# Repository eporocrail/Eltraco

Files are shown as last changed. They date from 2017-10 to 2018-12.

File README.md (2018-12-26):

  Aim is to develop a switching and signaling system for model railroad track control.
  Communication is wireless.

  To disconnect the decoder from the controlling software in space and time the MOSQUITTO
  MQTT broker is used.

  Hardware setup is as simple as possible. In stead of having one hardware module for diffferent applications
  the design aims for three different PCB's specific to task where the Wemos has to be slotted into.

  Sofware is modularised. It is gathered into one software package. The functionality of each separate decoder
  is configured by means of a website genrated by the decoder.

  *********************************************************************************************

  Target platform is Wemos D1 mini.

  11 digital input/output pins, all pins have interrupt/pwm/I2C/one-wire supported(except D0)
  1 analog input(3.2V max input)
  a Micro USB connection
  compatible with Arduino IDE.
  pins are active LOW but the Arduino IDE inverts this.

  All of the IO pins run at 3.3V:
  A levelshifter or voltage divider is required.

  For a relay a pin is followed by a transistor/IC. A relay is driven with 5V.

  For a sensor or servo each pin is followed by a 330R resistor to limit current to 10 mA.

  eltraco decoder     Function

  eltraco sensor decoder    Scanning 9 sensors
  eltraco switch decoder    Controlling 8 outputs
  eltraco turnout decoder   Controlling 2 turnouts

  GPIO usage:

  Decoder  pins     function

  Sensor   D0 .. D7     digital sensor
  
           A0           analogue sensor

  Switch   D0 .. D7     output (switch)

  Double   D0    relais 1
  
  Turnout  D1    current detector 1
           
           D2    current detector 2
           
           D3    not used
           
           D4    not used
           
           D5    relais 2
           
           D6    servo 1
           
           D7    servo 2
           
           D8    not used
           
           A0    not used
           
  Single   D0    relais 1
  
  Turnout  D1    current detector 1
           
           D2    sensor
           
           D3    sensor
           
           D4    sensor
           
           D5    sensor
           
           D6    servo 1
           
           D7    not used
           
           D8    not used
           
           A0    not used         

  ROCNET PROTOCOL

  packet payload content:
  byte 1  : groupId
  
  byte 2  : receiveIdH
  
  byte 3  : receiveIdL
  
  byte 4  : sendIdH
  
  byte 5  : sendIdL
  
  byte 6  : group
  
  byte 7  : code
  
  byte 8  : length
  
  byte 9  : data1
  
  byte 10 : data2
  
  byte 11 : data3
  
  byte 12 : data4

  --byte 1 only used for large network. Normally 0.

  --byte 2 only used when more than 255 decoders. Normally 0.

  --byte 3 Rocrail Server default Id is 1

  Broadcast Id = 0
  
  Decoder   Id = 2 ... 255   Not used for switching decoder

  --byte 4 only used when more than 255 decoders. Normally 0.

  --byte 5 Rocrail Server default Id is 1

  Decoder Id   = 2 ... 255 with restrictions as described under "addressing"

  --byte 6

  groups
  code   description     remark                     MQTT topic
  
  0      Host            Rocrail                    rocnet/ht
  
  7      Clock Fast      Clock                      rocnet/ck
  
  8      Sensor          Position determination     rocnet/sr
  
  9      Output                                     rocnet/ot

  --byte 7

  Code:  bit 7 = 0
  
     bit 6 and bit 5 represent Type of code
     
     bit 4 .. 0:  5 bit command 0 .. 31

  Type: 0 - test
  
  1 - request
  
  2 - event
  
  3 - reply

  Sensor

  Actions
  code description data 1  data 2  data 3  data 4  data n
  1    report      addrH¹  addrL¹  status  port    identifier (RFID)

  ¹) Address of the reporting loco.
  The sensor ID is set in the header; Sender.

  Output

  Type   Value
  
  switch   0
  
  light    1
  
  servo    2

  Actions
  code description data 1  data 2  data 3
  
  0      off       type    value   address
  
  1      on        type    value   address

  --byte 8 Netto number of following data bytes.

  At a speed of 200 KmH a loc runs 64 mm per second in scale H0 and 35 mm per second in scale N.
  To come to a reliable detection reaction a point sensor must be scanned at least 20 times per second in H0
  and at least 10 times per second in scale N.

  For scale H0 scan delay should be not larger than 50 miliseconds and for scale N not larger
  than 100 miliseconds. Default will be 20.

  The Wemos Module needs no 3.3V power supply. To the 5V pin external powersupply can be connected.

  Addressing:

  Addressing falls apart in a WiFi address, being an IP-address and a Rocnet address.

  Rocnet:

  In the Rocnet protocol (IdH*256 + IdL) represents the Rocnet Node Number. This number ranges from 1 .. 65536.
  It represents the "Bus" number.
  Depending on the function performed the I/O pin of the decoder is addressed with "data3" for
  "output" functions or "data4" for "sensor" functions. Turnouts are controlled with an "output" function.
  The values of data3/data4 are in rocrail inserted in field "Address"

  For eltraco an I/O pin is addressed by the combination of receiveIdL and data3/data4.
  This way each individual pin of each individual decoder can be addressed.

  A second way to address an IO pin is using a "fixed" receiveIdL and discriminating by means of data3/data4.
  Using this method provides in eltraco the possibility to address 255 turnouts by a consecutive number only.
  The default receiveIdL of Rocrail is "9". This receiveIdL is used to control turnouts. These addresses are
  used by the servo-tool to adjust the servo of a turnout.

  IP-address:
  The following IP-adress range is available:
  192.168.xxx.xxx

  IP-addres: Router 192.168.xxx.251
  
             Configuration website 192.168.xxx.252
             
             Command Station       192.168.xxx.253
             
             Mosquitto             192.168.xxx.254

  For the decoders are available 192.168.xxx.2 - 192.168.2.250

  Each decoder is allocated a unique IP-address out of the range 192.168.xxx.2 - 192.168.2.250.
  The last triplet is the Rocrail "Bus" number.

  Single turnout decoder:

Each decoder controls 1 turnout and reports occupation of it.

For the turnout decoder occupation of the turnout is reported at "Address" 1.

Table: Switches tab Interface - the last part of the IP-address is inserted into field "Bus"
       "1" is inserted into field "Address".
       e.g. (192.168.0.154 turnout is inserted as Bus 154 Address 1)

Table: Sensor tab Interface - the last part of the IP-address is inserted into field "Bus"
       "1" is inserted into field "Address". The external sensors report using "Address" numbers 2 .. 5.
       e.g. (192.168.0.154 turnout is inserted as Bus 154 Address 1, the second external sensor of the same
       decoder is inserted as Bus 154 Address 3)

Double turnout decoder:

Each decoder controls 2 turnouts and reports occupation of them.

For the turnout decoder occupation of the first turnout is reported at "Address" 1 and of the second
turnout at "Address" 2.

Table: Switches tab Interface - the last part of the IP-address is inserted into field "Bus"
       For the first turnout "1" is inserted into field "Address". For the second one "2" is inserted
       e.g. (192.168.0.154 turnout 2 is inserted as Bus 154 Address 2)

Table: Sensor tab Interface - the last part of the IP-address is inserted into field "Bus"
       For the first turnout "1" is inserted into field "Address". For the second one "2" is inserted
       e.g. (192.168.0.154 turnout 2 is inserted as Bus 154 Address 2)

Operation

During testing it turned out that move orders from Rocrail arrived so fast that an ongoing movement was
interrupted. To cater for this, incoming turnout orders are stored into a buffer. When ongoing movement is concluded,
buffer content is converted into a turnout order and the next turnout starts moving.

Sensor decoder:
Each decoder has eight digital and one analogue sensor.

The sensors report using "Address" numbers 1 .. 9.
Use of the analogue sensor is to be programmed by the user.

Table: Sensor tab Interface - the last part of the IP-address is inserted into field "Bus"
       port number is inserted into field "Address"
       e.g. (192.168.0.076 sensor 5 is inserted as Bus 76 Address 5)

Operation

The state of the sensor is controlled by interrupt. Not only the state of the sensor but also the point in time of activation is stored.
If the sensor is still in the activated state after the debounce period has passed the Sensor Message is sent. 
The state of the sensor will change to "inactive" by interrupt. After the minimum activation time has passed this inactive state is signalled 
with a Sensor Message.

Interrupt reacts on changes to drive the sensor state.

D0 can NOT be used with Interrupt. This reduces the amount of interrupt driven sensors per module to 7. (D1 .. D7).

D0 has to be watched with "polling".

Switch decoder
Each decoder has eight outputs.

Each decoder is allocated a unique IP-address out of the range 192.168.xxx.2 - 192.168.2.250.
The last triplet is the Rocrail "Bus" number.

The outputs are switched using "Address" numbers 1 .. 8.

Table: Switches tab Interface - the last part of the IP-address is inserted into field "Bus"
       The individual port number is inserted into field "Address"
       e.g. (192.168.0.201 port 3 is inserted as Bus 201 Address 3)

Operation

Via configuration it is possible to have an output switched ON during 200 mSec. An additional relais attached to that
output can be used to control a solenoid activated device.

To signal the state of a switch, a sensor message is transmitted after each switch action. 

Configuration of decoder

The Wemos module can be used in "ST" mode and "AP" mode simultaneously.
In "ST" mode it is possible to login onto an existing WiFi network for normal operations.
In "AP" mode it is possible to generate its own WiFi network. This network is used for configuration of the decoder.
Each module has its own configuration webserver on a shared WiFi configuration network with its own IP address.

The websever is based on the "EmbAJAX" library. This library facilitates dataexchange between webserver on the decoder
and a browser on a client. The user experience is as much as possible comparable with webservers on PC like hardware.

Configuration data and servo angles are stored in EEPROM.
Allocation of EEPROM memory to variables has to be planned.
  location variable
      0    AngleA1
      1    AngleB1
      2    Delay1
      3    Swap1
      4    AngleA2
      5    AngleB2
      6    Delay2
      7    Swap2
      8    decoderType
      9    debugFlag

  GENERALOFFSET+ 0 .. 25 ST WiFi SSID
  
  GENERALOFFSET + SSIDOFFSET + 0 .. 8 ST WiFi Password
  
  GENERALOFFSET + SSIDOFFSET + PWDOFFSET + 0 .. 6 ST WiFi IP address triplets
  
  GENERALOFFSET + SSIDOFFSET + PWDOFFSET + IPOFFSET + 0 .. 8 Output puls 
  
  GENERALOFFSET + SSIDOFFSET + PWDOFFSET + IPOFFSET + OUTPUTOFFSET + 0 .. 8 Switch active puls length
  
  GENERALOFFSET + SSIDOFFSET + PWDOFFSET + IPOFFSET + OUTPUTOFFSET + PULSLENGTHOFFSET+ 0 .. 8 Output sensor message

  GENERALOFFSET      - 20
  SSIDOFFSET         - 30
  PWDOFFSET          - 20
  IPOFFSET           - 10
  OUTPUTOFFSET        -10
  PULSLENGTHOFFSET    -20
  OUTPUTSENSOROFFSET  -10

The ST WiFi password is generated out of "ELTRACO" and the decoderId.
The AP WiFi SSID is generated out of "ELTRACO" and the decoderID. This also aplies to the related password.

There are two ways to transfer Software to the decoder.
Via USB cable and after inital software installation also "Over The Air"(OTA).
Each decoder has its own OTA name which is generated outof "ELTRACO" and the decoderId.

Author: E. Postma

November 2018

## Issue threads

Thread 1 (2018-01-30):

Where is  "user_interface.h"?

dagnall53, 2018-01-30:
The code for the servo setting tool looks very interesting, but I missed / cannot find "user_interface.h"
Can you add it to the repository or add a note to say where it is?
Many thanks
Dagnall

eporocrail, 2018-01-31:
Dagnall,
Thanks for the remark. You got me! It is a remnant which needs to be done away with.
I am working on a new version of the software, one single software package for all types of decoder. In that version it is not present anymore.
Ellard

Closed 2018-01-31.

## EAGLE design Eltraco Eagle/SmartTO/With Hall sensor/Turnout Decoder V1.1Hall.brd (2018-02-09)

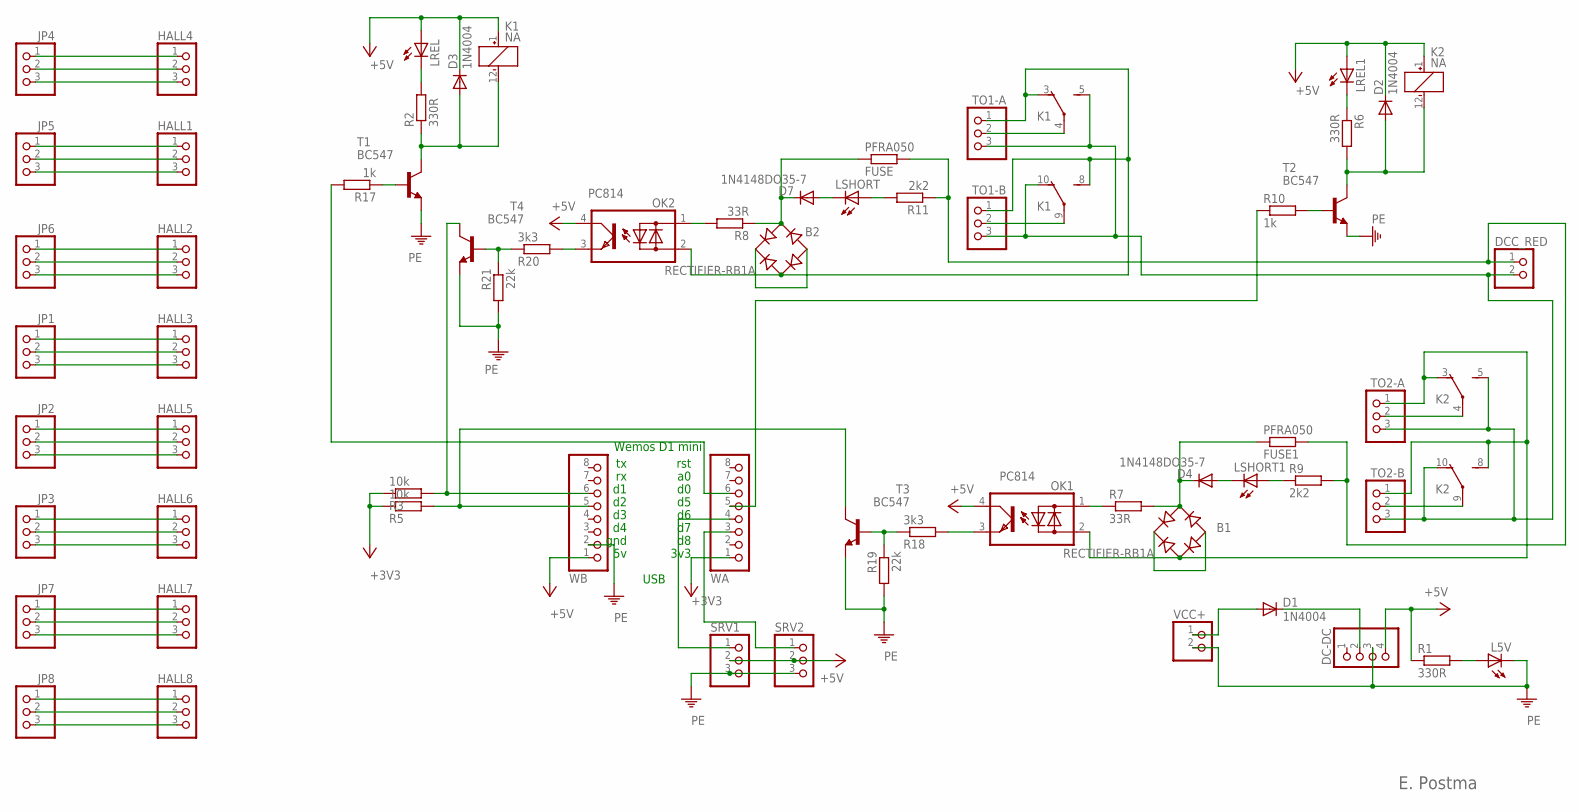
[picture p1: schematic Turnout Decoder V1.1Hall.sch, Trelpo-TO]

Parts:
B1, B2: RECTIFIER-RB1A; RB1A
D1, D2, D3: 1N4004; DO41-10
D4, D7: 1N4148DO35-7; DO35-7
DC-DC: PINHD-1X4; 1X04
DCC_RED: PINHD-1X2; 1X02
FUSE, FUSE1: PFRA050; 0414V
HALL1, HALL2, HALL3, HALL4, HALL5, HALL6, HALL7, HALL8: PINHD-1X3; 1X03
JP1, JP2, JP3, JP4, JP5, JP6, JP7, JP8: PINHD-1X3; 1X03
K1, K2: NA
L5V: LED3MM
LREL, LREL1: LED3MM
LSHORT, LSHORT1: LED3MM
OK1, OK2: PC814; DIL04
R1, R2, R6: 330R; 0207/7
R3, R5: 10k; 0207/7
R7, R8: 33R; 0207/7
R9, R11: 2k2; 0207/7
R10, R17: 1k; 0207/7
R18, R20: 3k3; 0207/7
R19, R21: 22k; 0207/7
SRV1, SRV2: PINHD-1X3; 1X03
T1, T2, T3, T4: BC547; TO92
TO1-A, TO1-B, TO2-A, TO2-B: PINHD-1X3; 1X03
VCC+: PINHD-1X2; 1X02
WA: PINHD-1X8; 1X08
WB: PINHD-1X8; 1X08

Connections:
+3V3: R3.1, R5.1, WA.1
+5V: D2.C, D3.C, DC-DC.4, K1.1 (+), K2.1 (+), LREL.A, LREL1.A, OK1.4 (C), OK2.4 (C), R1.1, SRV1.2, SRV2.2, WB.1
unnamed: HALL1.2, JP5.2
unnamed: LREL1.K (C), R6.1
unnamed: DCC_RED.1, FUSE.2, FUSE1.2, R9.2, R11.1
unnamed: D1.A, VCC+.1
unnamed: OK1.1 (AC1), R7.1
unnamed: LSHORT1.A, R9.1
unnamed: D4.A, LSHORT1.K (C)
unnamed: D2.A, K2.12 (-), R6.2, T2.3 (C)
unnamed: R10.2, T2.2 (B)
unnamed: B1.+, B1.-
unnamed: OK1.3 (E), R18.2
unnamed: LREL.K (C), R2.2
unnamed: K2.4, TO2-A.2
unnamed: B2.AC2, K1.3 (O), K1.8 (S), OK2.2 (AC2), TO1-A.1, TO1-B.1
unnamed: K2.9, TO2-B.2
unnamed: DCC_RED.2, K1.5 (S), K1.10 (O), K2.5 (S), K2.10 (O), TO1-A.3, TO1-B.3, TO2-A.3, TO2-B.3
unnamed: OK2.3 (E), R20.2
unnamed: B1.AC2, K2.3 (O), K2.8 (S), OK1.2 (AC2), TO2-A.1, TO2-B.1
unnamed: R3.2, T4.3 (C), WB.6
unnamed: B1.AC1, D4.C, FUSE1.1, R7.2
unnamed: OK2.1 (AC1), R8.2
unnamed: R5.2, T3.3 (C), WB.5
unnamed: B2.AC1, D7.C, FUSE.1, R8.1
unnamed: HALL1.1, JP5.1
unnamed: HALL1.3, JP5.3
unnamed: K1.4, TO1-A.2
unnamed: R18.1, R19.1, T3.2 (B)
unnamed: R20.1, R21.1, T4.2 (B)
unnamed: R17.2, WA.6
unnamed: HALL2.2, JP6.2
unnamed: SRV1.1, WA.4
unnamed: K1.9, TO1-B.2
unnamed: SRV2.1, WA.3
unnamed: R10.1, WA.5
unnamed: LSHORT.A, R11.2
unnamed: HALL2.1, JP6.1
unnamed: HALL2.3, JP6.3
unnamed: HALL3.2, JP1.2
unnamed: HALL3.1, JP1.1
unnamed: HALL3.3, JP1.3
unnamed: D7.A, LSHORT.K (C)
unnamed: B2.+, B2.-
unnamed: HALL5.2, JP2.2
unnamed: HALL5.1, JP2.1
unnamed: HALL5.3, JP2.3
unnamed: L5V.A, R1.2
unnamed: HALL6.2, JP3.2
unnamed: HALL6.1, JP3.1
unnamed: R17.1, T1.2 (B)
unnamed: D3.A, K1.12 (-), R2.1, T1.3 (C)
unnamed: HALL6.3, JP3.3
unnamed: HALL7.2, JP7.2
unnamed: HALL7.1, JP7.1
unnamed: HALL7.3, JP7.3
unnamed: HALL4.2, JP4.2
unnamed: HALL4.3, JP4.3
unnamed: HALL4.1, JP4.1
unnamed: D1.C, DC-DC.2
unnamed: HALL8.2, JP8.2
unnamed: HALL8.1, JP8.1
unnamed: HALL8.3, JP8.3
PE: DC-DC.3, L5V.K (C), R19.2, R21.2, SRV1.3, SRV2.3, T1.1 (E), T2.1 (E), T3.1 (E), T4.1 (E), VCC+.2, WB.2

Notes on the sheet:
rst
3v3
Wemos D1 mini
gnd
USB
E. Postma

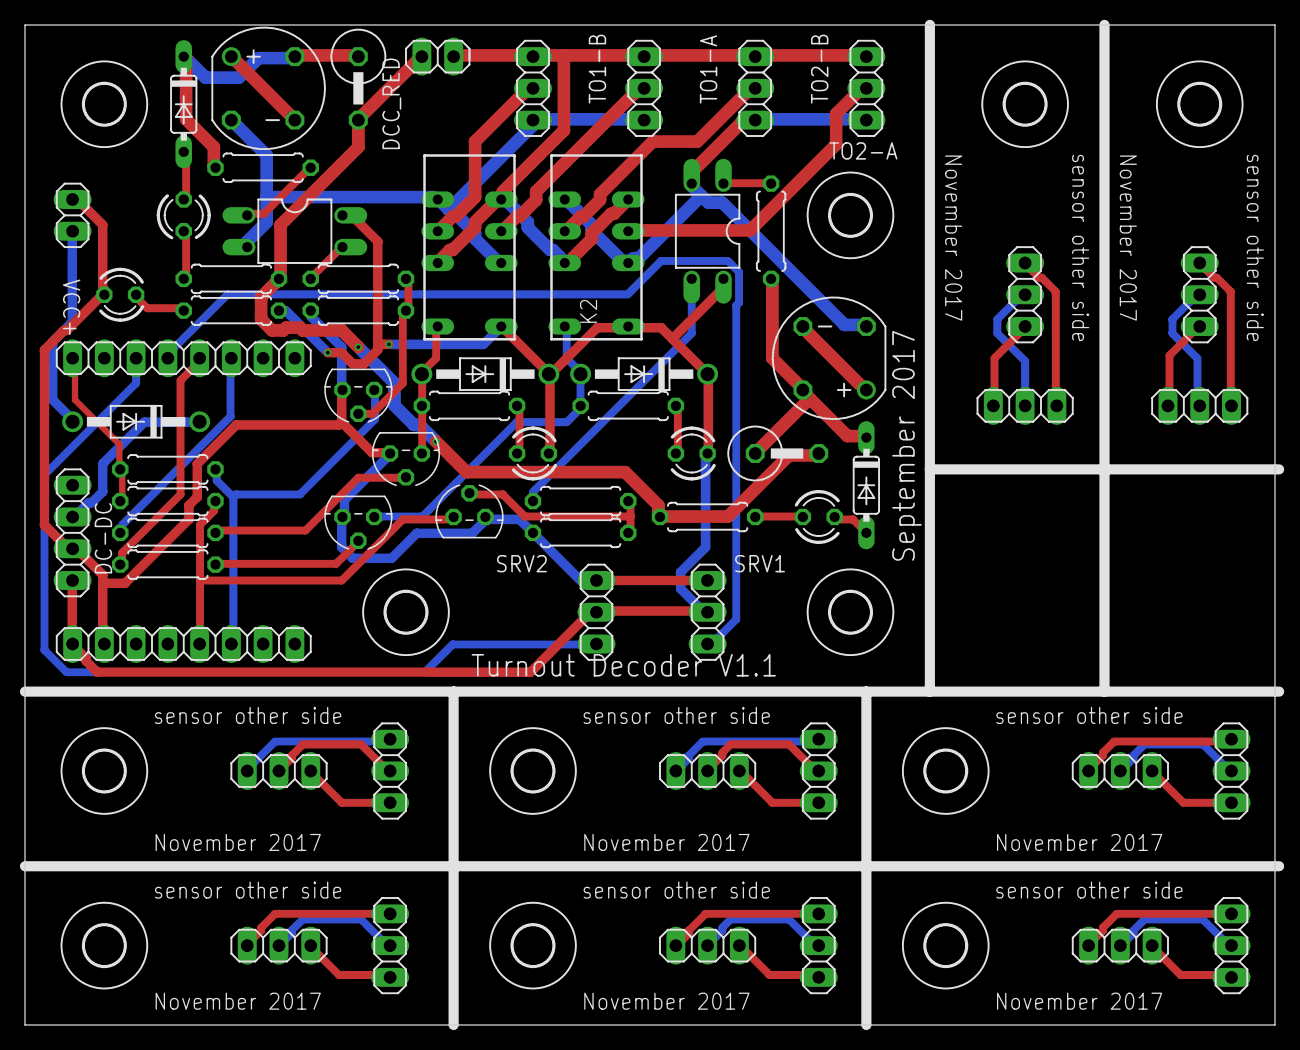
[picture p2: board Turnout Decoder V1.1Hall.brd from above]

Board: 2 copper layers, 100.0 x 80.0 mm, 76 parts (0 on the bottom side), 64 nets.

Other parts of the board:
U$1, U$2, U$3, U$4, U$5, U$6, U$7, U$11, U$12, U$14, U$15, U$16: 3,2

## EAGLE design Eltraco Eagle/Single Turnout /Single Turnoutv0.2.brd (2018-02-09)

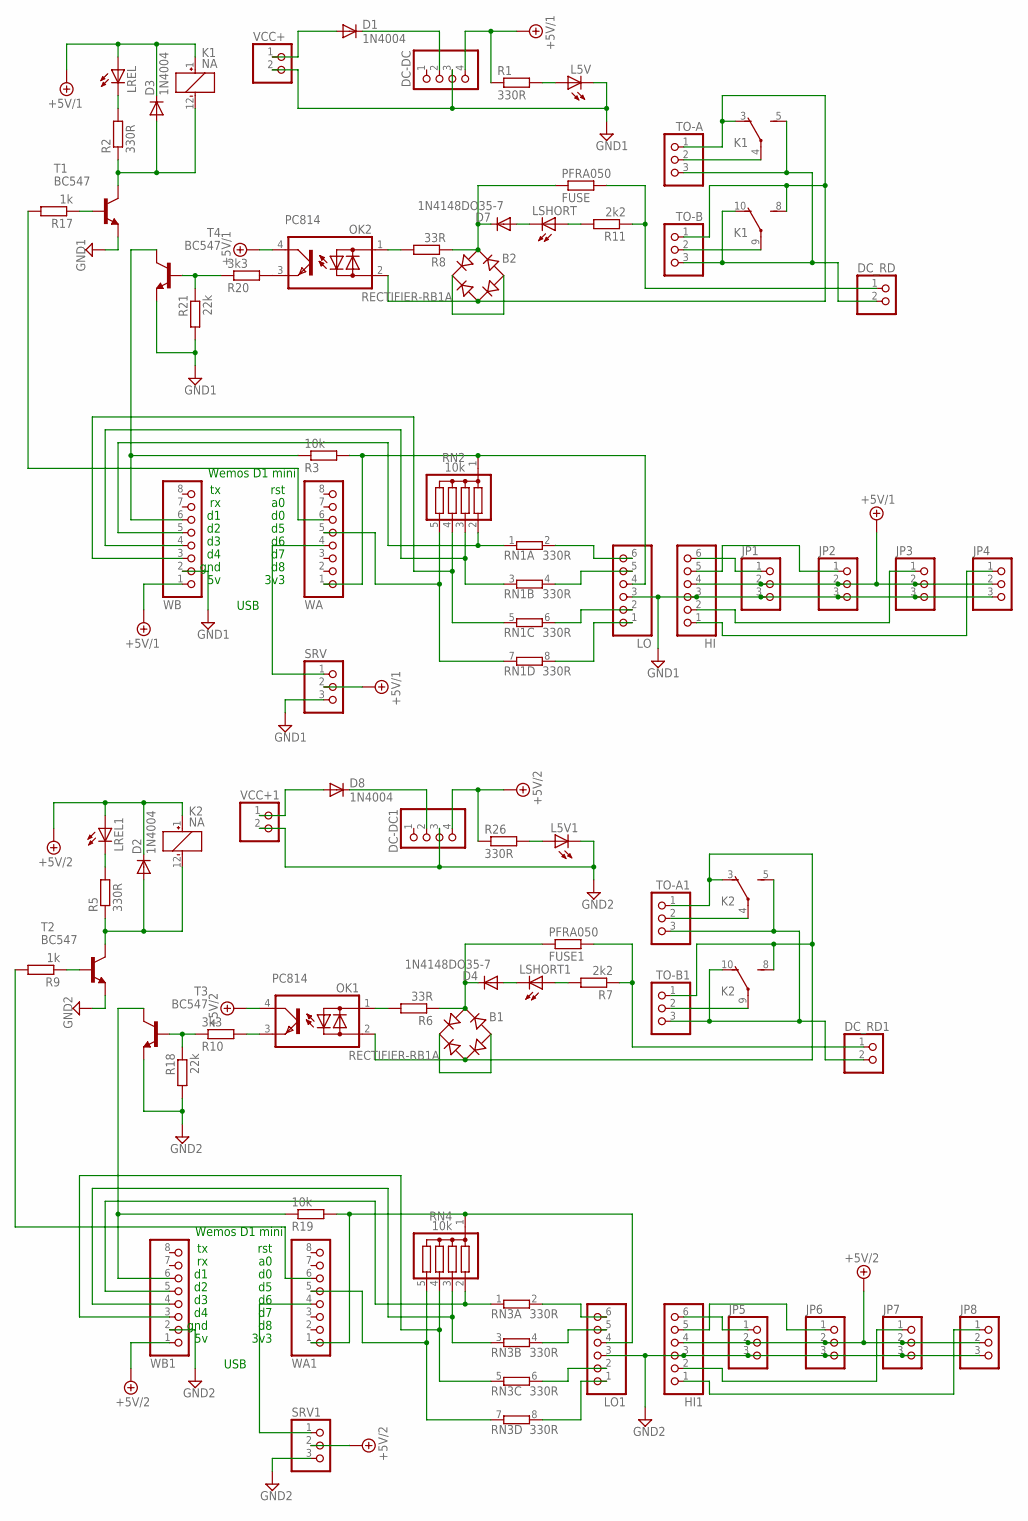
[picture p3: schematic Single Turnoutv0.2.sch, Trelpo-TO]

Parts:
B1, B2: RECTIFIER-RB1A; RB1A
D1, D2, D3, D8: 1N4004; DO41-10
D4, D7: 1N4148DO35-7; DO35-7
DC-DC, DC-DC1: PINHD-1X4; 1X04
DC_RD, DC_RD1: PINHD-1X2; 1X02
FUSE, FUSE1: PFRA050; 0414V
HI, HI1: PINHD-1X6; 1X06
JP1, JP2, JP3, JP4, JP5, JP6, JP7, JP8: PINHD-1X3; 1X03
K1, K2: NA
L5V, L5V1: LED3MM
LO, LO1: PINHD-1X6; 1X06
LREL, LREL1: LED3MM
LSHORT, LSHORT1: LED3MM
OK1, OK2: PC814; DIL04
R1, R2, R5, R26: 330R; 0207/7
R3, R19: 10k; 0207/7
R6, R8: 33R; 0207/7
R7, R11: 2k2; 0207/7
R9, R17: 1k; 0207/7
R10, R20: 3k3; 0207/7
R18, R21: 22k; 0207/7
RN1, RN3: 330R; SIL8
RN2, RN4: 10k; SIL5
SRV, SRV1: PINHD-1X3; 1X03
T1, T2, T3, T4: BC547; TO92
TO-A, TO-A1: PINHD-1X3; 1X03
TO-B, TO-B1: PINHD-1X3; 1X03
VCC+, VCC+1: PINHD-1X2; 1X02
WA, WA1: PINHD-1X8; 1X08
WB, WB1: PINHD-1X8; 1X08

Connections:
+5V/1: D3.C, DC-DC.4, HI.4, JP1.2, JP2.2, JP3.2, JP4.2, K1.1 (+), LREL.A, OK2.4 (C), R1.1, SRV.2, WB.1
+5V/2: D2.C, DC-DC1.4, HI1.4, JP5.2, JP6.2, JP7.2, JP8.2, K2.1 (+), LREL1.A, OK1.4 (C), R26.1, SRV1.2, WB1.1
GND1: DC-DC.3, HI.3, JP1.3, JP2.3, JP3.3, JP4.3, L5V.K (C), LO.3, R21.2, SRV.3, T1.1 (E), T4.1 (E), VCC+.2, WB.2
GND2: DC-DC1.3, HI1.3, JP5.3, JP6.3, JP7.3, JP8.3, L5V1.K (C), LO1.3, R18.2, SRV1.3, T2.1 (E), T3.1 (E), VCC+1.2, WB1.2
unnamed: LO.4, R3.2, RN2.1, WA.1
unnamed: LO.6, RN1.2
unnamed: DC_RD.1, FUSE.2, R11.1
unnamed: D1.A, VCC+.1
unnamed: R3.1, T4.3 (C), WB.6
unnamed: LREL1.K (C), R5.2
unnamed: OK1.1 (AC1), R6.2
unnamed: LSHORT1.A, R7.2
unnamed: D4.A, LSHORT1.K (C)
unnamed: D2.A, K2.12 (-), R5.1, T2.3 (C)
unnamed: R9.1, T2.2 (B)
unnamed: LREL.K (C), R2.2
unnamed: B1.+, B1.-
unnamed: B2.AC2, K1.3 (O), K1.8 (S), OK2.2 (AC2), TO-A.1, TO-B.1
unnamed: K2.4, TO-A1.2
unnamed: DC_RD.2, K1.5 (S), K1.10 (O), TO-A.3, TO-B.3
unnamed: OK2.3 (E), R20.2
unnamed: K2.9, TO-B1.2
unnamed: B1.AC2, K2.3 (O), K2.8 (S), OK1.2 (AC2), TO-A1.1, TO-B1.1
unnamed: B1.AC1, D4.C, FUSE1.1, R6.1
unnamed: OK2.1 (AC1), R8.2
unnamed: DC_RD1.2, K2.5 (S), K2.10 (O), TO-A1.3, TO-B1.3
unnamed: B2.AC1, D7.C, FUSE.1, R8.1
unnamed: LO.5, RN1.4 (2)
unnamed: HI.2, JP3.1
unnamed: K1.4, TO-A.2
unnamed: DC_RD1.1, FUSE1.2, R7.1
unnamed: R20.1, R21.1, T4.2 (B)
unnamed: R17.2, WA.6
unnamed: HI.5, JP2.1
unnamed: SRV.1, WA.4
unnamed: K1.9, TO-B.2
unnamed: SRV1.1, WA1.4
unnamed: R10.1, R18.1, T3.2 (B)
unnamed: LSHORT.A, R11.2
unnamed: HI.6, JP1.1
unnamed: RN1.3 (1), RN2.3, WB.4
unnamed: RN1.1, RN2.2, WB.5
unnamed: HI1.2, JP7.1
unnamed: HI1.5, JP6.1
unnamed: D7.A, LSHORT.K (C)
unnamed: B2.+, B2.-
unnamed: HI1.6, JP5.1
unnamed: RN1.5 (1), RN2.4, WB.3
unnamed: RN1.7 (1), RN2.5, WA.5
unnamed: L5V.A, R1.2
unnamed: RN3.5 (1), RN4.4, WB1.3
unnamed: LO1.4, R19.2, RN4.1, WA1.1
unnamed: R17.1, T1.2 (B)
unnamed: D3.A, K1.12 (-), R2.1, T1.3 (C)
unnamed: RN3.7 (1), RN4.5, WA1.5
unnamed: HI1.1, JP8.1
unnamed: LO.2, RN1.6 (2)
unnamed: RN3.3 (1), RN4.3, WB1.4
unnamed: RN3.1, RN4.2, WB1.5
unnamed: LO.1, RN1.8 (2)
unnamed: LO1.6, RN3.2
unnamed: D1.C, DC-DC.2
unnamed: LO1.5, RN3.4 (2)
unnamed: LO1.2, RN3.6 (2)
unnamed: HI.1, JP4.1
unnamed: R9.2, WA1.6
unnamed: OK1.3 (E), R10.2
unnamed: L5V1.A, R26.2
unnamed: R19.1, T3.3 (C), WB1.6
unnamed: LO1.1, RN3.8 (2)
unnamed: D8.A, VCC+1.1
unnamed: D8.C, DC-DC1.2

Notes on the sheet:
rst
3v3
Wemos D1 mini
gnd
USB

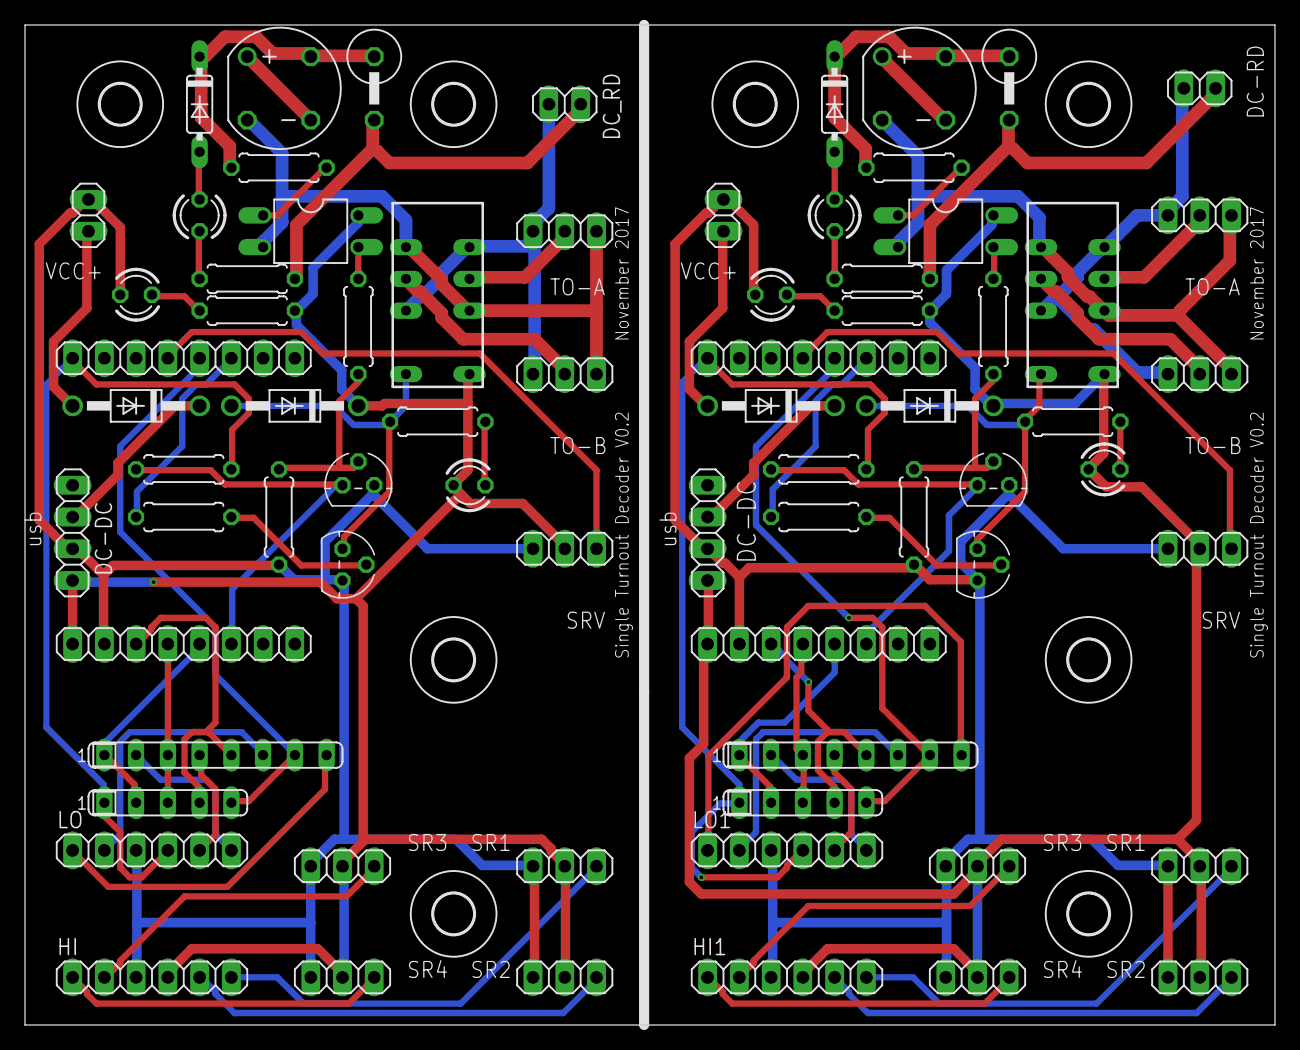
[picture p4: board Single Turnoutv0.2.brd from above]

Board: 2 copper layers, 100.0 x 80.0 mm, 80 parts (0 on the bottom side), 72 nets.

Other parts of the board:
U$1, U$2, U$3, U$4, U$5, U$6, U$7, U$9: 3,2

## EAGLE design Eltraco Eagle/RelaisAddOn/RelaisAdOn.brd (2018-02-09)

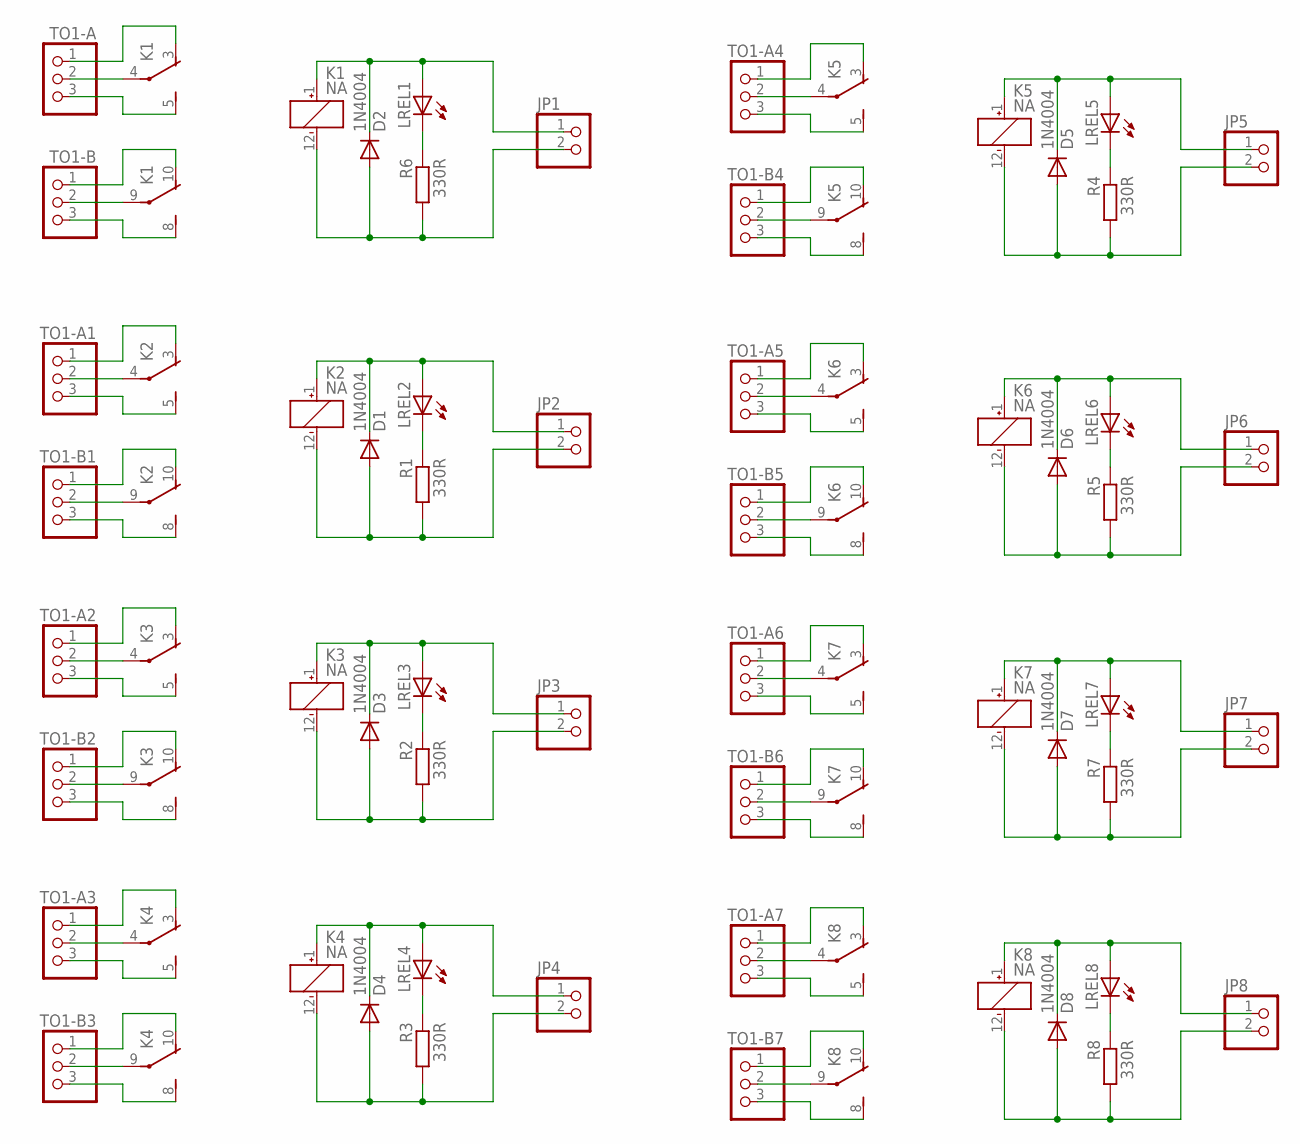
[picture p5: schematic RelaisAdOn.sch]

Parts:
D1, D2, D3, D4, D5, D6, D7, D8: 1N4004; DO41-10
JP1, JP2, JP3, JP4, JP5, JP6, JP7, JP8: PINHD-1X2; 1X02
K1, K2, K3, K4, K5, K6, K7, K8: NA
LREL1, LREL2, LREL3, LREL4, LREL5, LREL6, LREL7, LREL8: LED3MM
R1, R2, R3, R4, R5, R6, R7, R8: 330R; 0207/7
TO1-A, TO1-A1, TO1-A2, TO1-A3, TO1-A4, TO1-A5, TO1-A6, TO1-A7, TO1-B, TO1-B1, TO1-B2, TO1-B3, TO1-B4, TO1-B5, TO1-B6, TO1-B7: PINHD-1X3; 1X03

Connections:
unnamed: K1.4, TO1-A.2
unnamed: LREL1.K (C), R6.1
unnamed: K1.9, TO1-B.2
unnamed: K1.8 (S), TO1-B.3
unnamed: K1.10 (O), TO1-B.1
unnamed: K1.3 (O), TO1-A.1
unnamed: K1.5 (S), TO1-A.3
unnamed: D2.A, JP1.2, K1.12 (-), R6.2
unnamed: D2.C, JP1.1, K1.1 (+), LREL1.A
unnamed: LREL2.K (C), R1.1
unnamed: D1.A, JP2.2, K2.12 (-), R1.2
unnamed: D1.C, JP2.1, K2.1 (+), LREL2.A
unnamed: K2.4, TO1-A1.2
unnamed: K2.9, TO1-B1.2
unnamed: K2.8 (S), TO1-B1.3
unnamed: K2.10 (O), TO1-B1.1
unnamed: K2.3 (O), TO1-A1.1
unnamed: K2.5 (S), TO1-A1.3
unnamed: LREL3.K (C), R2.1
unnamed: D3.A, JP3.2, K3.12 (-), R2.2
unnamed: D3.C, JP3.1, K3.1 (+), LREL3.A
unnamed: K3.4, TO1-A2.2
unnamed: K3.9, TO1-B2.2
unnamed: K3.8 (S), TO1-B2.3
unnamed: K3.10 (O), TO1-B2.1
unnamed: K3.3 (O), TO1-A2.1
unnamed: K3.5 (S), TO1-A2.3
unnamed: LREL4.K (C), R3.1
unnamed: D4.A, JP4.2, K4.12 (-), R3.2
unnamed: D4.C, JP4.1, K4.1 (+), LREL4.A
unnamed: K4.4, TO1-A3.2
unnamed: K4.9, TO1-B3.2
unnamed: K4.8 (S), TO1-B3.3
unnamed: K4.10 (O), TO1-B3.1
unnamed: K4.3 (O), TO1-A3.1
unnamed: K4.5 (S), TO1-A3.3
unnamed: LREL5.K (C), R4.1
unnamed: D5.A, JP5.2, K5.12 (-), R4.2
unnamed: D5.C, JP5.1, K5.1 (+), LREL5.A
unnamed: K5.4, TO1-A4.2
unnamed: K5.9, TO1-B4.2
unnamed: K5.8 (S), TO1-B4.3
unnamed: K5.10 (O), TO1-B4.1
unnamed: K5.3 (O), TO1-A4.1
unnamed: K5.5 (S), TO1-A4.3
unnamed: LREL6.K (C), R5.1
unnamed: D6.A, JP6.2, K6.12 (-), R5.2
unnamed: D6.C, JP6.1, K6.1 (+), LREL6.A
unnamed: K6.4, TO1-A5.2
unnamed: K6.9, TO1-B5.2
unnamed: K6.8 (S), TO1-B5.3
unnamed: K6.10 (O), TO1-B5.1
unnamed: K6.3 (O), TO1-A5.1
unnamed: K6.5 (S), TO1-A5.3
unnamed: LREL7.K (C), R7.1
unnamed: D7.A, JP7.2, K7.12 (-), R7.2
unnamed: D7.C, JP7.1, K7.1 (+), LREL7.A
unnamed: K7.4, TO1-A6.2
unnamed: K7.9, TO1-B6.2
unnamed: K7.8 (S), TO1-B6.3
unnamed: K7.10 (O), TO1-B6.1
unnamed: K7.3 (O), TO1-A6.1
unnamed: K7.5 (S), TO1-A6.3
unnamed: LREL8.K (C), R8.1
unnamed: D8.A, JP8.2, K8.12 (-), R8.2
unnamed: D8.C, JP8.1, K8.1 (+), LREL8.A
unnamed: K8.4, TO1-A7.2
unnamed: K8.9, TO1-B7.2
unnamed: K8.8 (S), TO1-B7.3
unnamed: K8.10 (O), TO1-B7.1
unnamed: K8.3 (O), TO1-A7.1
unnamed: K8.5 (S), TO1-A7.3

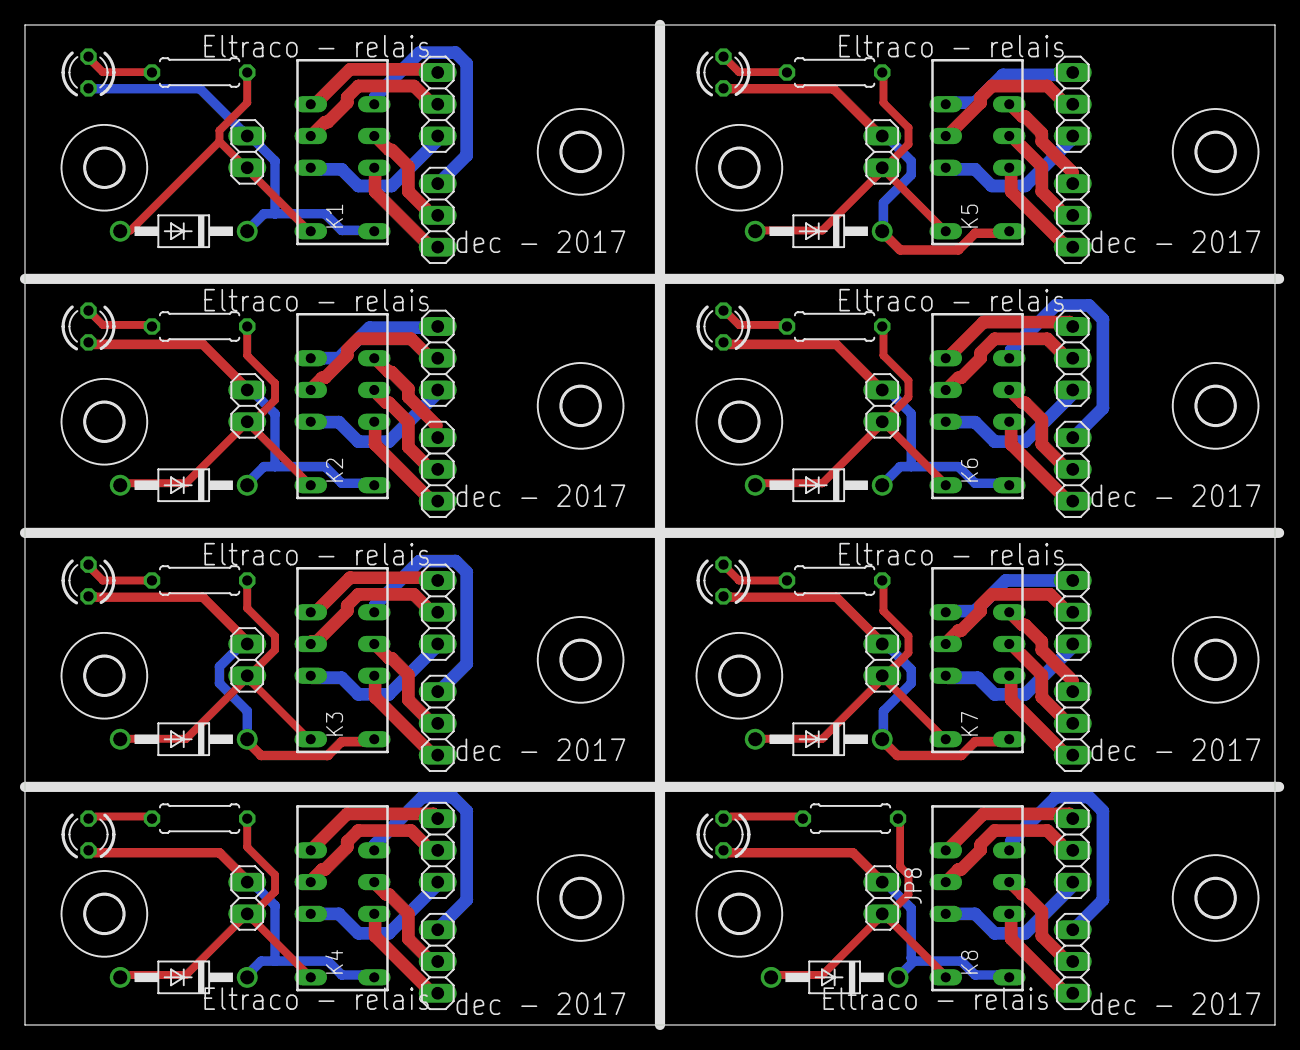
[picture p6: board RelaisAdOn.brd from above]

Board: 2 copper layers, 100.0 x 80.0 mm, 72 parts (0 on the bottom side), 72 nets.

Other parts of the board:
U$1, U$2, U$3, U$4, U$5, U$6, U$7, U$8, U$9, U$10, U$11, U$12, U$13, U$14, U$15, U$16: 3,0

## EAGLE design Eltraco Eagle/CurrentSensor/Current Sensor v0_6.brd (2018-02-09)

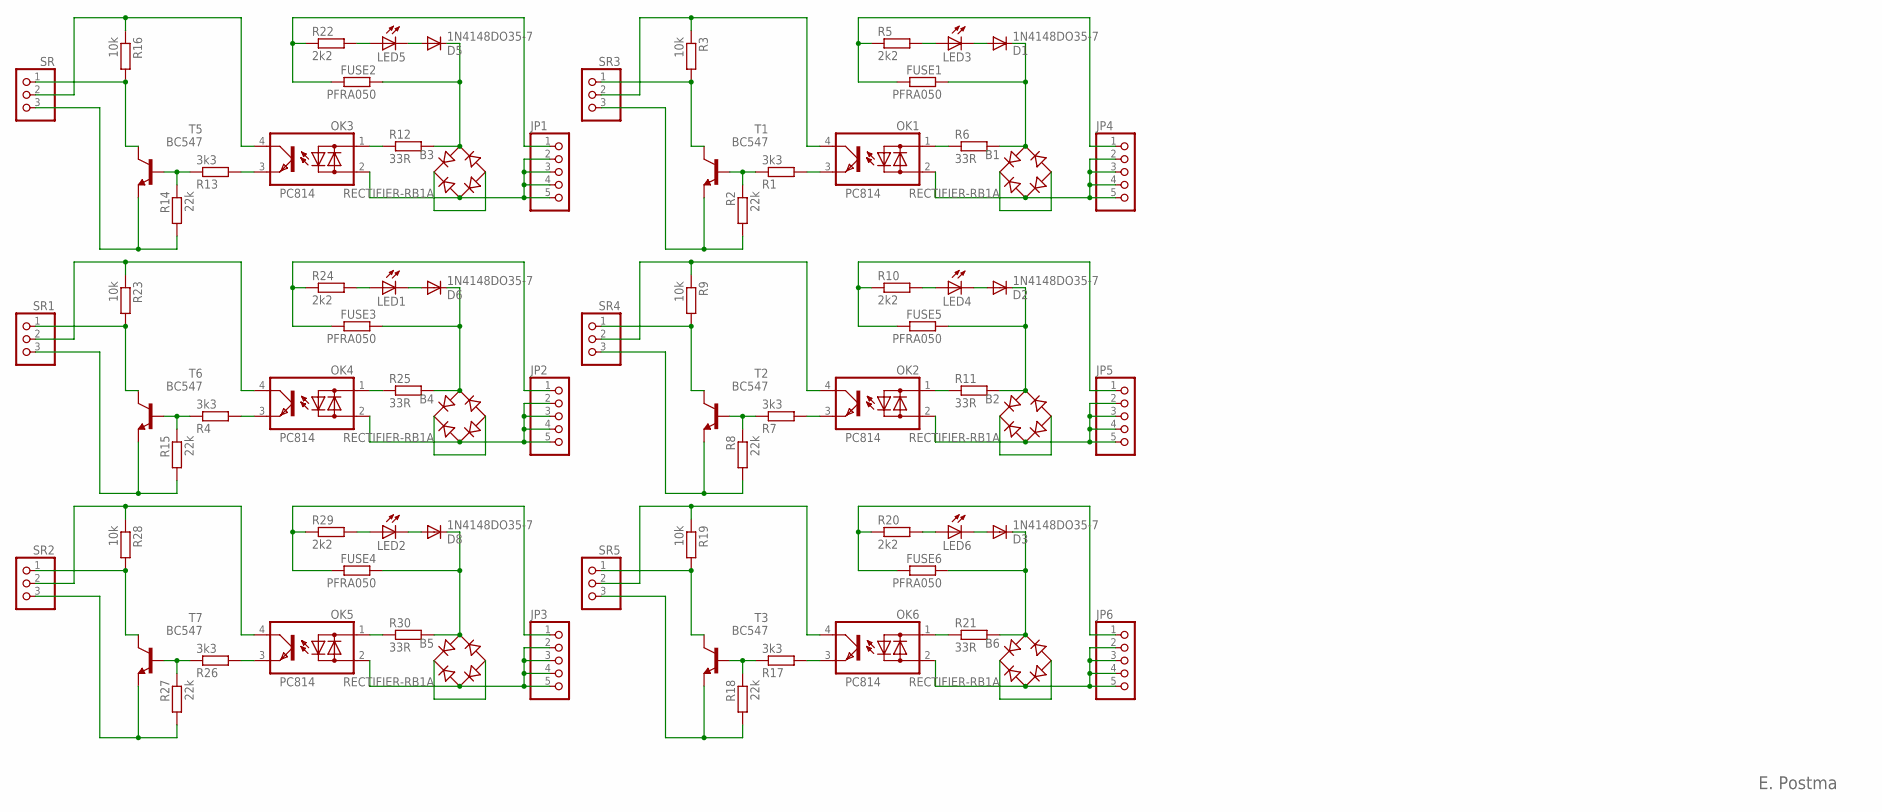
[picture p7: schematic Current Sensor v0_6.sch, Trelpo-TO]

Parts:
B1, B2, B3, B4, B5, B6: RECTIFIER-RB1A; RB1A
D1, D2, D3, D5, D6, D8: 1N4148DO35-7; DO35-7
FUSE1, FUSE2, FUSE3, FUSE4, FUSE5, FUSE6: PFRA050; 0414V
JP1, JP2, JP3, JP4, JP5, JP6: PINHD-1X5; 1X05
LED1, LED2, LED3, LED4, LED5, LED6: LED3MM
OK1, OK2, OK3, OK4, OK5, OK6: PC814; DIL04
R1, R4, R7, R13, R17, R26: 3k3; 0207/7
R2, R8, R14, R15, R18, R27: 22k; 0207/7
R3, R9, R16, R19, R23, R28: 10k; 0207/7
R5, R10, R20, R22, R24, R29: 2k2; 0207/7
R6, R11, R12, R21, R25, R30: 33R; 0207/7
SR, SR1, SR2, SR3, SR4, SR5: PINHD-1X3; 1X03
T1, T2, T3, T5, T6, T7: BC547; TO92

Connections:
unnamed: OK3.1 (AC1), R12.1
unnamed: OK1.1 (AC1), R6.1
unnamed: LED3.A, R5.2
unnamed: D1.A, LED3.K (C)
unnamed: B1.AC1, D1.C, FUSE1.1, R6.2
unnamed: B1.+, B1.-
unnamed: FUSE1.2, JP4.1, R5.1
unnamed: B1.AC2, JP4.2, JP4.3, JP4.4, JP4.5, OK1.2 (AC2)
unnamed: R1.1, R2.1, T1.2 (B)
unnamed: R3.2, SR3.1, T1.3 (C)
unnamed: OK1.3 (E), R1.2
unnamed: OK1.4 (C), R3.1, SR3.2
unnamed: R2.2, SR3.3, T1.1 (E)
unnamed: OK2.1 (AC1), R11.1
unnamed: LED4.A, R10.2
unnamed: D2.A, LED4.K (C)
unnamed: B2.AC1, D2.C, FUSE5.1, R11.2
unnamed: B2.+, B2.-
unnamed: FUSE5.2, JP5.1, R10.1
unnamed: B2.AC2, JP5.2, JP5.3, JP5.4, JP5.5, OK2.2 (AC2)
unnamed: R7.1, R8.1, T2.2 (B)
unnamed: R9.2, SR4.1, T2.3 (C)
unnamed: OK2.3 (E), R7.2
unnamed: LED5.A, R22.2
unnamed: D5.A, LED5.K (C)
unnamed: OK2.4 (C), R9.1, SR4.2
unnamed: R8.2, SR4.3, T2.1 (E)
unnamed: OK6.1 (AC1), R21.1
unnamed: LED6.A, R20.2
unnamed: B3.AC1, D5.C, FUSE2.1, R12.2
unnamed: D3.A, LED6.K (C)
unnamed: B6.AC1, D3.C, FUSE6.1, R21.2
unnamed: B6.+, B6.-
unnamed: FUSE6.2, JP6.1, R20.1
unnamed: B6.AC2, JP6.2, JP6.3, JP6.4, JP6.5, OK6.2 (AC2)
unnamed: B3.+, B3.-
unnamed: FUSE2.2, JP1.1, R22.1
unnamed: R13.1, R14.1, T5.2 (B)
unnamed: R16.2, SR.1, T5.3 (C)
unnamed: B3.AC2, JP1.2, JP1.3, JP1.4, JP1.5, OK3.2 (AC2)
unnamed: R17.1, R18.1, T3.2 (B)
unnamed: R19.2, SR5.1, T3.3 (C)
unnamed: OK3.3 (E), R13.2
unnamed: OK4.1 (AC1), R25.1
unnamed: OK3.4 (C), R16.1, SR.2
unnamed: OK6.3 (E), R17.2
unnamed: LED1.A, R24.2
unnamed: D6.A, LED1.K (C)
unnamed: OK6.4 (C), R19.1, SR5.2
unnamed: R18.2, SR5.3, T3.1 (E)
unnamed: B4.AC1, D6.C, FUSE3.1, R25.2
unnamed: B4.+, B4.-
unnamed: FUSE3.2, JP2.1, R24.1
unnamed: B4.AC2, JP2.2, JP2.3, JP2.4, JP2.5, OK4.2 (AC2)
unnamed: R4.1, R15.1, T6.2 (B)
unnamed: R23.2, SR1.1, T6.3 (C)
unnamed: OK4.3 (E), R4.2
unnamed: OK4.4 (C), R23.1, SR1.2
unnamed: R14.2, SR.3, T5.1 (E)
unnamed: R15.2, SR1.3, T6.1 (E)
unnamed: OK5.1 (AC1), R30.1
unnamed: LED2.A, R29.2
unnamed: D8.A, LED2.K (C)
unnamed: B5.AC1, D8.C, FUSE4.1, R30.2
unnamed: B5.+, B5.-
unnamed: FUSE4.2, JP3.1, R29.1
unnamed: B5.AC2, JP3.2, JP3.3, JP3.4, JP3.5, OK5.2 (AC2)
unnamed: R26.1, R27.1, T7.2 (B)
unnamed: R28.2, SR2.1, T7.3 (C)
unnamed: OK5.3 (E), R26.2
unnamed: OK5.4 (C), R28.1, SR2.2
unnamed: R27.2, SR2.3, T7.1 (E)

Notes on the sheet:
E. Postma

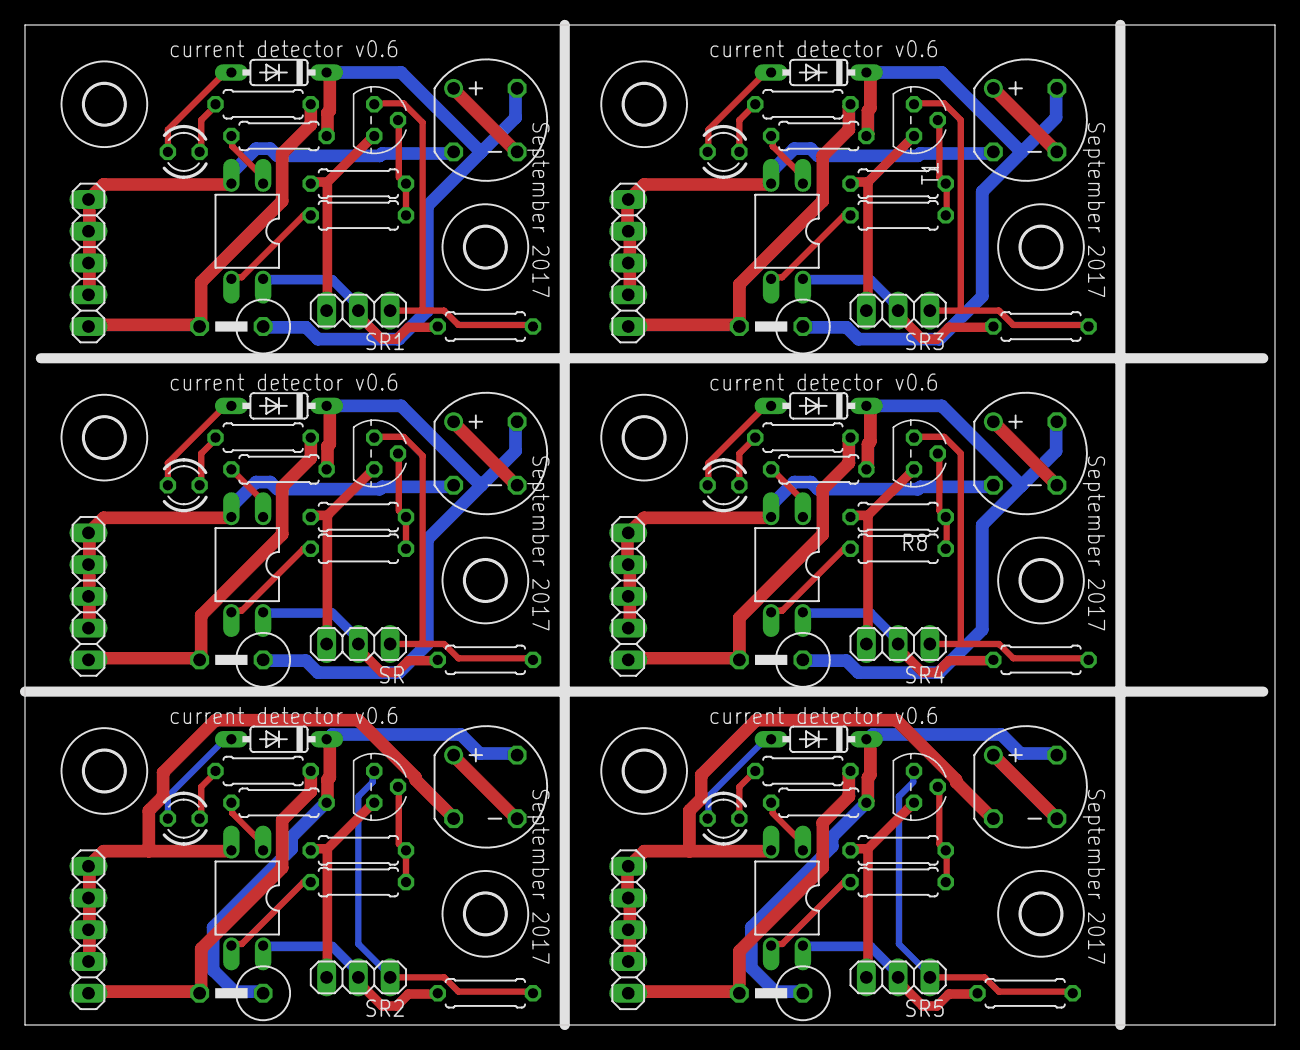
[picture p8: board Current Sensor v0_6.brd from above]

Board: 2 copper layers, 100.0 x 80.0 mm, 90 parts (0 on the bottom side), 72 nets.

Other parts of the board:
U$1, U$2, U$3, U$4, U$5, U$6, U$7, U$8, U$9, U$10, U$11, U$12: 3,2

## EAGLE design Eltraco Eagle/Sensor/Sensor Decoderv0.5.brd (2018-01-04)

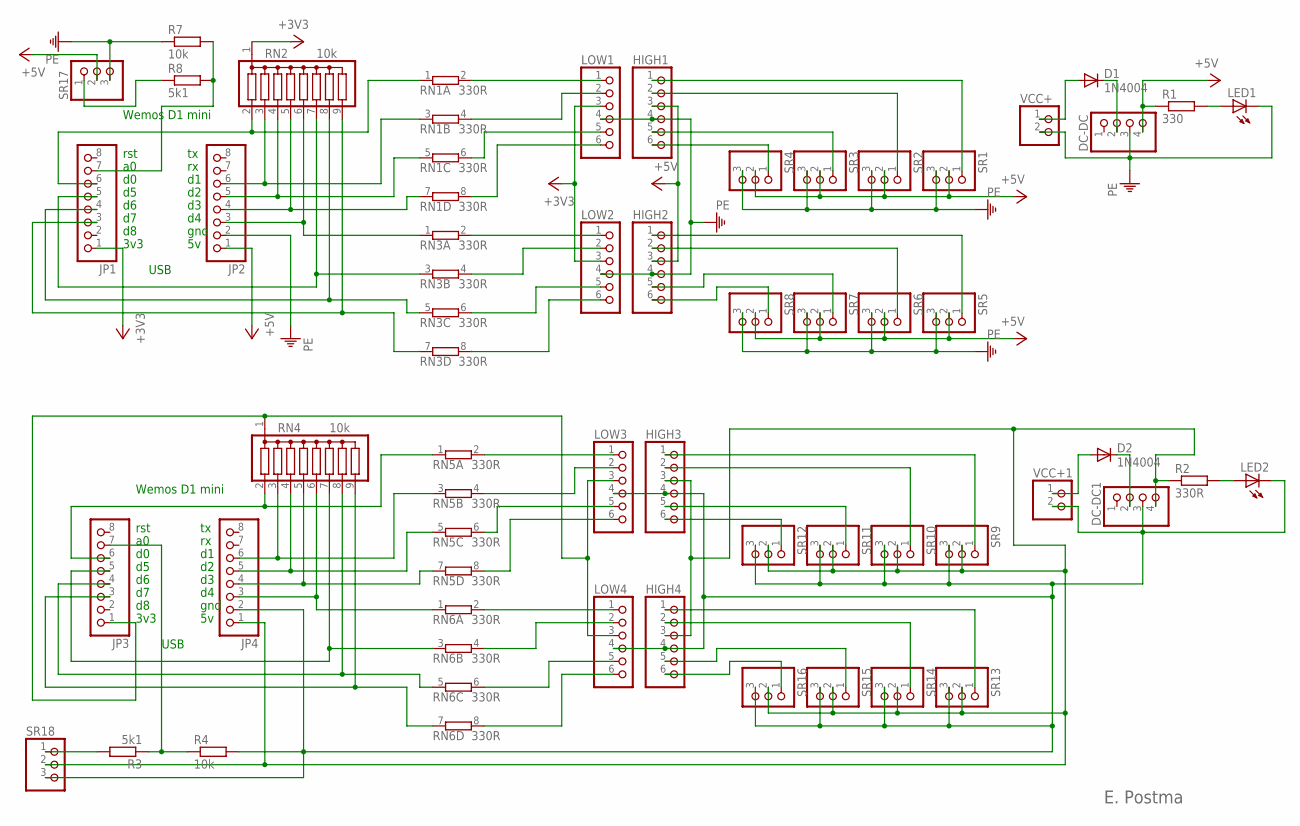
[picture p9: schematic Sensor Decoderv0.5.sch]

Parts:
D1, D2: 1N4004; DO41-10
DC-DC, DC-DC1: PINHD-1X4; 1X04
HIGH1, HIGH2, HIGH3, HIGH4: PINHD-1X6; 1X06
JP1, JP2, JP3, JP4: PINHD-1X8; 1X08
LED1, LED2: LED3MM
LOW1, LOW2, LOW3, LOW4: PINHD-1X6; 1X06
R1: 330; 0207/7
R2: 330R; 0207/7
R3, R8: 5k1; 0207/7
R4, R7: 10k; 0207/7
RN1, RN3, RN5, RN6: 330R; SIL8
RN2, RN4: 10k; SIL9
SR1, SR2, SR3, SR4, SR5, SR6, SR7, SR8, SR9, SR10, SR11, SR12, SR13, SR14, SR15, SR16, SR17, SR18: PINHD-1X3; 1X03
VCC+, VCC+1: PINHD-1X2; 1X02

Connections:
+3V3: JP1.1, LOW1.3, LOW2.3, RN2.1
+5V: DC-DC.4, HIGH1.3, HIGH2.3, JP2.1, R1.1, SR1.2, SR2.2, SR3.2, SR4.2, SR5.2, SR6.2, SR7.2, SR8.2, SR17.2
unnamed: HIGH2.6, SR8.1
unnamed: JP1.6, RN1.1, RN2.2
unnamed: JP1.4, RN2.8, RN3.5 (1)
unnamed: D1.C, DC-DC.2
unnamed: JP1.5, RN2.7, RN3.3 (1)
unnamed: LED1.A, R1.2
unnamed: JP2.5, RN1.5 (1), RN2.4
unnamed: HIGH2.5, SR7.1
unnamed: JP2.3, RN2.6, RN3.1
unnamed: JP2.6, RN1.3 (1), RN2.3
unnamed: JP1.3, RN2.9, RN3.7 (1)
unnamed: LOW1.1, RN1.2
unnamed: JP2.4, RN1.7 (1), RN2.5
unnamed: HIGH1.6, SR4.1
unnamed: HIGH1.5, SR3.1
unnamed: HIGH1.2, SR2.1
unnamed: HIGH1.1, SR1.1
unnamed: HIGH2.2, SR6.1
unnamed: HIGH2.1, SR5.1
unnamed: JP3.6, RN4.2, RN5.1
unnamed: LED2.A, R2.2
unnamed: JP4.6, RN4.3, RN5.3 (1)
unnamed: JP4.5, RN4.4, RN5.5 (1)
unnamed: JP4.4, RN4.5, RN5.7 (1)
unnamed: D2.A, VCC+1.1
unnamed: D2.C, DC-DC1.2
unnamed: JP4.3, RN4.6, RN6.1
unnamed: JP3.5, RN4.7, RN6.3 (1)
unnamed: JP3.4, RN4.8, RN6.5 (1)
unnamed: JP3.3, RN4.9, RN6.7 (1)
unnamed: LOW3.1, RN5.2
unnamed: LOW3.2, RN5.4 (2)
unnamed: LOW3.5, RN5.6 (2)
unnamed: LOW3.6, RN5.8 (2)
unnamed: LOW4.1, RN6.2
unnamed: LOW4.2, RN6.4 (2)
unnamed: LOW4.5, RN6.6 (2)
unnamed: LOW4.6, RN6.8 (2)
unnamed: HIGH4.6, SR16.1
unnamed: HIGH4.5, SR15.1
unnamed: HIGH4.2, SR14.1
unnamed: HIGH4.1, SR13.1
unnamed: HIGH3.6, SR12.1
unnamed: LOW1.2, RN1.4 (2)
unnamed: LOW1.5, RN1.6 (2)
unnamed: LOW1.6, RN1.8 (2)
unnamed: D1.A, VCC+.1
unnamed: LOW2.1, RN3.2
unnamed: LOW2.2, RN3.4 (2)
unnamed: LOW2.5, RN3.6 (2)
unnamed: LOW2.6, RN3.8 (2)
unnamed: HIGH3.5, SR11.1
unnamed: HIGH3.2, SR10.1
unnamed: HIGH3.1, SR9.1
unnamed: DC-DC1.4, HIGH3.3, HIGH4.3, JP4.1, R2.1, SR9.2, SR10.2, SR11.2, SR12.2, SR13.2, SR14.2, SR15.2, SR16.2, SR18.2
unnamed: JP3.1, LOW3.3, LOW4.3, RN4.1
unnamed: DC-DC1.3, HIGH3.4, HIGH4.4, JP4.2, LED2.K (C), LOW3.4, LOW4.4, R4.2, SR9.3, SR10.3, SR11.3, SR12.3, SR13.3, SR14.3, SR15.3, SR16.3, SR18.3, VCC+1.2
unnamed: JP1.7, R7.2, R8.2
unnamed: JP3.7, R3.1, R4.1
unnamed: R3.2, SR18.1
unnamed: R8.1, SR17.1
PE: DC-DC.3, HIGH1.4, HIGH2.4, JP2.2, LED1.K (C), LOW1.4, LOW2.4, R7.1, SR1.3, SR2.3, SR3.3, SR4.3, SR5.3, SR6.3, SR7.3, SR8.3, SR17.3, VCC+.2

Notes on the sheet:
rst
3v3
Wemos D1 mini
gnd
USB
E. Postma

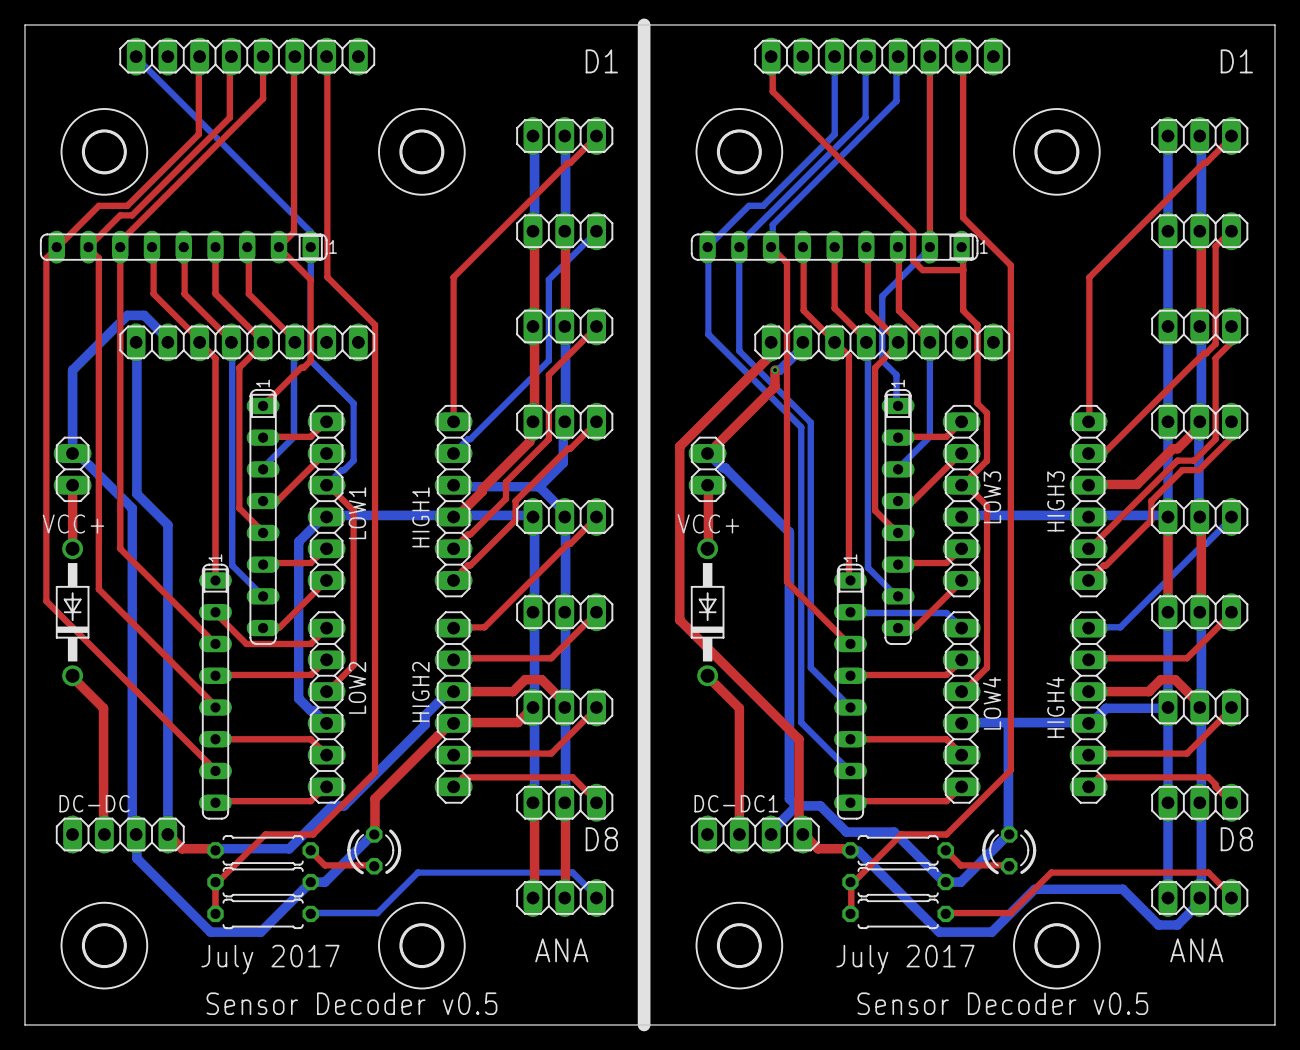
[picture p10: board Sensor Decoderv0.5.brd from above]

Board: 2 copper layers, 100.0 x 80.0 mm, 58 parts (0 on the bottom side), 64 nets.

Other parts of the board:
U$1, U$2, U$3, U$4, U$5, U$6, U$7, U$8: 3,2

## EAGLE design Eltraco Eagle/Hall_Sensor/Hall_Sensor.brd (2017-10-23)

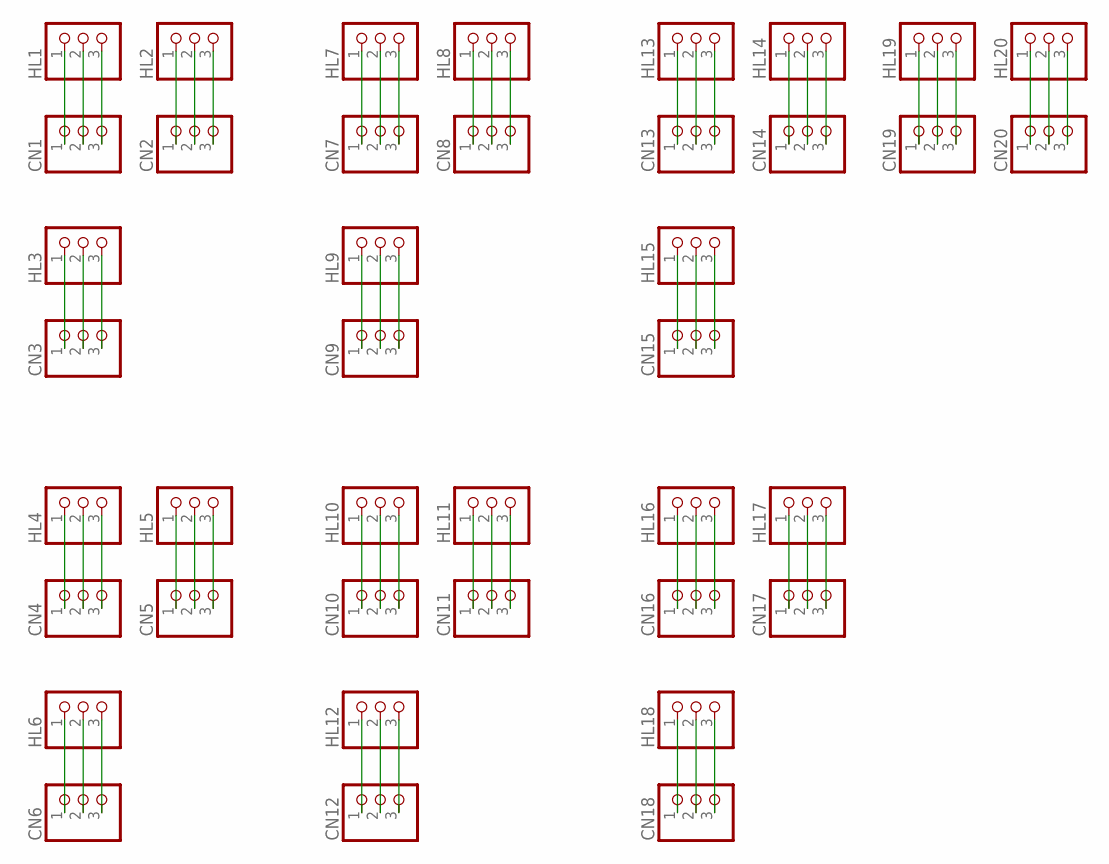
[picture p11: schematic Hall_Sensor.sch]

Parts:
CN1, CN2, CN3, CN4, CN5, CN6, CN7, CN8, CN9, CN10, CN11, CN12, CN13, CN14, CN15, CN16, CN17, CN18, CN19, CN20: PINHD-1X3; 1X03
HL1, HL2, HL3, HL4, HL5, HL6, HL7, HL8, HL9, HL10, HL11, HL12, HL13, HL14, HL15, HL16, HL17, HL18, HL19, HL20: PINHD-1X3; 1X03

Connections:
unnamed: CN7.1, HL7.1
unnamed: CN7.2, HL7.2
unnamed: CN7.3, HL7.3
unnamed: CN8.1, HL8.1
unnamed: CN8.2, HL8.2
unnamed: CN8.3, HL8.3
unnamed: CN9.1, HL9.1
unnamed: CN9.2, HL9.2
unnamed: CN9.3, HL9.3
unnamed: CN10.1, HL10.1
unnamed: CN10.2, HL10.2
unnamed: CN10.3, HL10.3
unnamed: CN11.1, HL11.1
unnamed: CN11.2, HL11.2
unnamed: CN11.3, HL11.3
unnamed: CN12.1, HL12.1
unnamed: CN12.2, HL12.2
unnamed: CN12.3, HL12.3
unnamed: CN13.1, HL13.1
unnamed: CN13.2, HL13.2
unnamed: CN13.3, HL13.3
unnamed: CN14.1, HL14.1
unnamed: CN14.2, HL14.2
unnamed: CN14.3, HL14.3
unnamed: CN15.1, HL15.1
unnamed: CN15.2, HL15.2
unnamed: CN15.3, HL15.3
unnamed: CN16.1, HL16.1
unnamed: CN16.2, HL16.2
unnamed: CN16.3, HL16.3
unnamed: CN17.1, HL17.1
unnamed: CN17.2, HL17.2
unnamed: CN17.3, HL17.3
unnamed: CN18.1, HL18.1
unnamed: CN18.2, HL18.2
unnamed: CN18.3, HL18.3
unnamed: CN19.1, HL19.1
unnamed: CN19.2, HL19.2
unnamed: CN19.3, HL19.3
unnamed: CN1.1, HL1.1
unnamed: CN20.1, HL20.1
unnamed: CN20.2, HL20.2
unnamed: CN20.3, HL20.3
unnamed: CN1.2, HL1.2
unnamed: CN1.3, HL1.3
unnamed: CN2.1, HL2.1
unnamed: CN2.2, HL2.2
unnamed: CN2.3, HL2.3
unnamed: CN3.1, HL3.1
unnamed: CN3.2, HL3.2
unnamed: CN3.3, HL3.3
unnamed: CN4.1, HL4.1
unnamed: CN4.2, HL4.2
unnamed: CN4.3, HL4.3
unnamed: CN5.1, HL5.1
unnamed: CN5.2, HL5.2
unnamed: CN5.3, HL5.3
unnamed: CN6.1, HL6.1
unnamed: CN6.2, HL6.2
unnamed: CN6.3, HL6.3

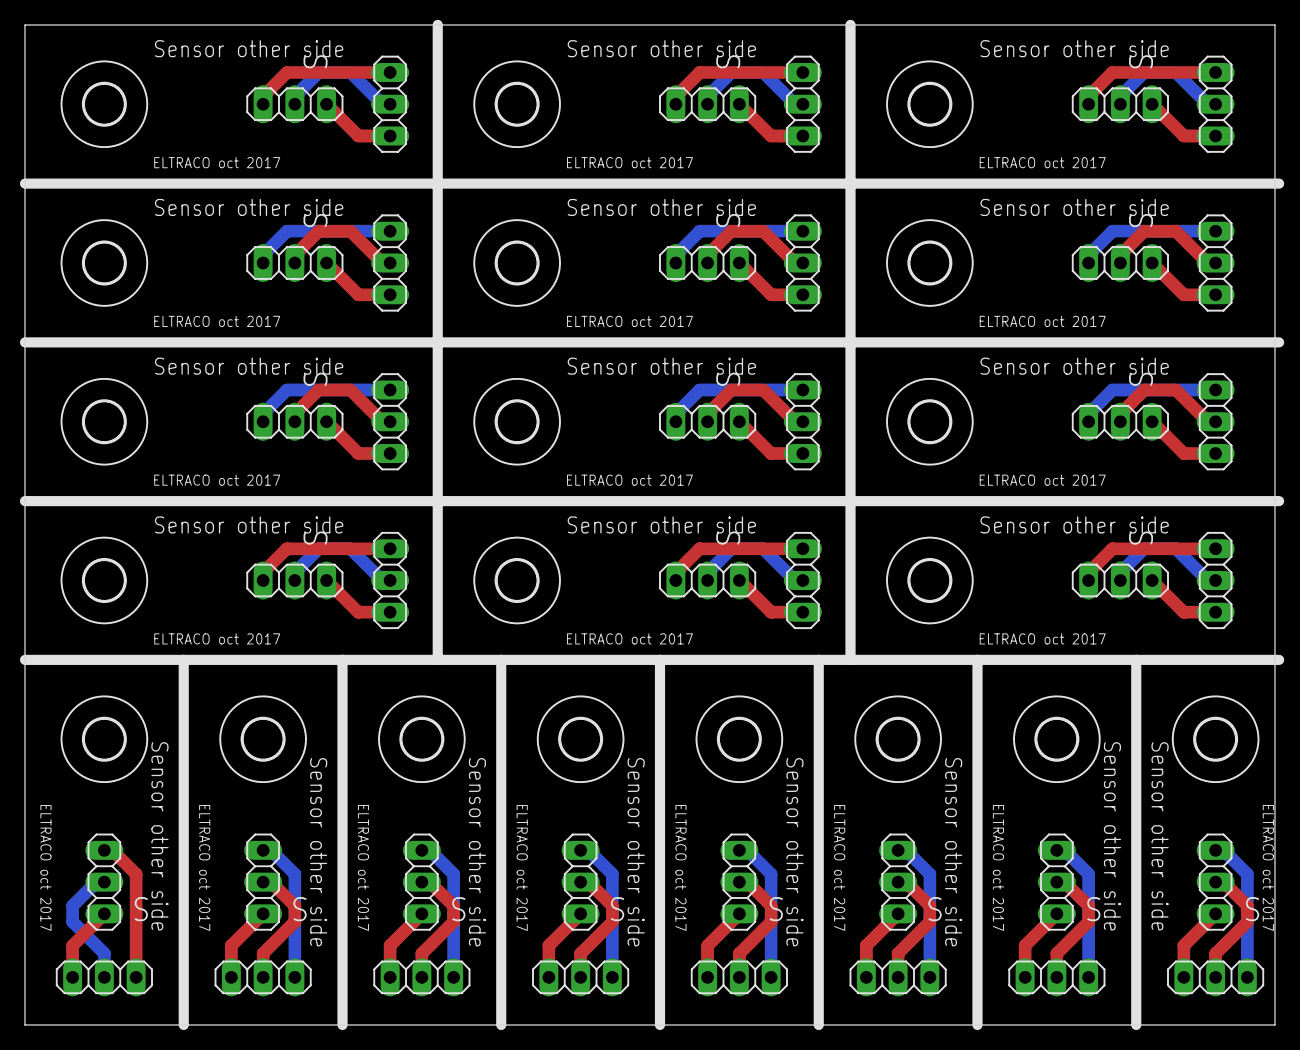
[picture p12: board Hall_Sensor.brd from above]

Board: 2 copper layers, 100.0 x 80.0 mm, 60 parts (0 on the bottom side), 60 nets.

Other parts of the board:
U$1, U$2, U$3, U$4, U$5, U$6, U$7, U$8, U$9, U$10, U$11, U$12, U$13, U$14, U$15, U$16, U$17, U$18, U$19, U$20: 3,2

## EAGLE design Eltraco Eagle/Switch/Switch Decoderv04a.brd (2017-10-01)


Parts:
1, 2, 3, 4, 5, 6, 7, 8, 9, 10, 11, 12, 13, 14, 15, 16, 17, 18, 19, 20, 21, 22, 23, 24: PINHD-1X2; 1X02
D1, D2, D3: 1N4004; DO41-10
DC-DC, DC-DC1, DC-DC2: PINHD-1X4; 1X04
IC1, IC2, IC3: ULN2803; DIL18
JP1, JP2, JP4, JP5, JP7, JP8: PINHD-1X8; 1X08
JP3, JP6, JP9: JP1E; JP1
LED1, LED2, LED3: LED3MM
POWER, POWER1, POWER2: PINHD-1X2; 1X02
R1, R2, R3: 1k; 0309/10
RN1, RN2, RN3, RN4, RN5, RN6: 330R; SIL8

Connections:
unnamed: DC-DC.3, IC1.9 (GND), JP2.2, LED1.K (C), POWER.2
unnamed: IC1.1 (I1), JP1.6
unnamed: IC1.7 (I7), JP1.4
unnamed: D1.C, DC-DC.2
unnamed: IC1.6 (I6), JP1.5
unnamed: LED1.A, R1.2
unnamed: IC1.3 (I3), JP2.5
unnamed: 1.1, 2.1, 3.1, 4.1, 5.1, 6.1, 7.1, 8.1, IC1.10 (CD+), JP3.2
unnamed: IC1.5 (I5), JP2.3
unnamed: IC1.2 (I2), JP2.6
unnamed: IC1.8 (I8), JP1.3
unnamed: IC1.18 (O1), RN1.1
unnamed: IC1.4 (I4), JP2.4
unnamed: IC2.1 (I1), JP4.6
unnamed: 1.2, RN1.2
unnamed: 9.1, 10.1, 11.1, 12.1, 13.1, 14.1, 15.1, 16.1, IC2.10 (CD+), JP6.2
unnamed: IC1.17 (O2), RN1.3 (1)
unnamed: 2.2, RN1.4 (2)
unnamed: 3.2, RN1.6 (2)
unnamed: IC1.16 (O3), RN1.5 (1)
unnamed: IC1.15 (O4), RN1.7 (1)
unnamed: 4.2, RN1.8 (2)
unnamed: 5.2, RN2.2
unnamed: IC1.14 (O5), RN2.1
unnamed: IC1.13 (O6), RN2.3 (1)
unnamed: 6.2, RN2.4 (2)
unnamed: 7.2, RN2.6 (2)
unnamed: IC1.12 (O7), RN2.5 (1)
unnamed: 8.2, RN2.8 (2)
unnamed: LED2.A, R2.2
unnamed: IC2.2 (I2), JP5.6
unnamed: IC2.3 (I3), JP5.5
unnamed: IC2.4 (I4), JP5.4
unnamed: D2.A, POWER1.1
unnamed: D2.C, DC-DC1.2
unnamed: IC2.5 (I5), JP5.3
unnamed: IC2.6 (I6), JP4.5
unnamed: IC2.7 (I7), JP4.4
unnamed: IC2.8 (I8), JP4.3
unnamed: IC3.18 (O1), RN5.1
unnamed: DC-DC1.3, IC2.9 (GND), JP5.2, LED2.K (C), POWER1.2
unnamed: IC1.11 (O8), RN2.7 (1)
unnamed: IC2.11 (O8), RN4.7 (1)
unnamed: IC2.18 (O1), RN3.1
unnamed: IC2.17 (O2), RN3.3 (1)
unnamed: 9.2, RN3.2
unnamed: D1.A, POWER.1
unnamed: 10.2, RN3.4 (2)
unnamed: IC2.16 (O3), RN3.5 (1)
unnamed: IC2.15 (O4), RN3.7 (1)
unnamed: 11.2, RN3.6 (2)
unnamed: 12.2, RN3.8 (2)
unnamed: IC2.14 (O5), RN4.1
unnamed: IC2.13 (O6), RN4.3 (1)
unnamed: 13.2, RN4.2
unnamed: 14.2, RN4.4 (2)
unnamed: IC2.12 (O7), RN4.5 (1)
unnamed: 15.2, RN4.6 (2)
unnamed: IC3.1 (I1), JP7.6
unnamed: LED3.A, R3.2
unnamed: IC3.2 (I2), JP8.6
unnamed: IC3.3 (I3), JP8.5
unnamed: IC3.4 (I4), JP8.4
unnamed: D3.A, POWER2.1
unnamed: D3.C, DC-DC2.2
unnamed: IC3.5 (I5), JP8.3
unnamed: IC3.6 (I6), JP7.5
unnamed: IC3.7 (I7), JP7.4
unnamed: IC3.8 (I8), JP7.3
unnamed: 17.1, 18.1, 19.1, 20.1, 21.1, 22.1, 23.1, 24.1, IC3.10 (CD+), JP9.2
unnamed: DC-DC2.3, IC3.9 (GND), JP8.2, LED3.K (C), POWER2.2
unnamed: 16.2, RN4.8 (2)
unnamed: IC3.11 (O8), RN6.7 (1)
unnamed: DC-DC.4, JP2.1, JP3.1, R1.1
unnamed: IC3.17 (O2), RN5.3 (1)
unnamed: DC-DC1.4, JP5.1, JP6.1, R2.1
unnamed: DC-DC2.4, JP8.1, JP9.1, R3.1
unnamed: IC3.16 (O3), RN5.5 (1)
unnamed: IC3.15 (O4), RN5.7 (1)
unnamed: 17.2, RN5.2
unnamed: IC3.14 (O5), RN6.1
unnamed: IC3.13 (O6), RN6.3 (1)
unnamed: 18.2, RN5.4 (2)
unnamed: 19.2, RN5.6 (2)
unnamed: IC3.12 (O7), RN6.5 (1)
unnamed: 20.2, RN5.8 (2)
unnamed: 21.2, RN6.2
unnamed: 22.2, RN6.4 (2)
unnamed: 23.2, RN6.6 (2)
unnamed: 24.2, RN6.8 (2)

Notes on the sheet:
rst
3v3
Wemos D1 mini
gnd
USB


Board: 2 copper layers, 100.0 x 80.0 mm, 66 parts (0 on the bottom side), 90 nets.

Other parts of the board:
U$1, U$2, U$3, U$4, U$5, U$6, U$7, U$8, U$9: 3,2

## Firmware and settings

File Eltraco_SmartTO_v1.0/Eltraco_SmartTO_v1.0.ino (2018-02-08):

/*
        This software is no longer supported. Replaced by one single package "eltraco"
    
  changelog:
  "2018-02-03" website for configuration decoder added. Single software package.

  changelog:
  "2017-12-21" Software version display added
              
  dec 2017-2
  "char" for numbers is WRONG!
  change to byte

  dec 2017:
  new MQTT library. supports qos2. link for library: https://github.com/Imroy/pubsubclient
  Length of MQTT outgoing message equal to Rocnet message length.
  "yield()" in loop.
  display of published and received messages on serial monitor harmonised.
  change "byte" to "char"


  Eltraco_SmartTO_v1.0
  Ready for publication

  /*************************************************************************************

  Aim is to develop a switching and signaling system for model railroad track control.
  Communication is wireless.

  To disconnect the decoder from the controlling software in space and time the MOSQUITTO
  MQTT broker is used.

  Hardware setup is as simple as possible. In stead of having one hardware module for diffferent applications
  the design aims for three different PCB's specific to task where the Wemos has to be slotted into.

  Sofware is modularised. Instead of having one sketch for diffferent applications the design aims for
  three different sketches specific to task.

  *********************************************************************************************

  Target platform is Wemos D1 mini.

  11 digital input/output pins, all pins have interrupt/pwm/I2C/one-wire supported(except D0)
  1 analog input(3.2V max input)
  a Micro USB connection
  compatible with Arduino IDE.
  pins are active LOW but the Arduino IDE inverts this.

  All of the IO pins run at 3.3V:
  A levelshifter or voltage divider is required.

  For a relay a pin is followed by a transistor/IC. A relay is driven with 5V.

  For a sensor or servo each pin is followed by a 330R resistor to limit current to 10 mA.

  eltraco decoder     Function

  eltraco sensor decoder    Scanning 9 sensors
  eltraco switch decoder    Controlling 8 outputs
  eltraco turnout decoder   Controlling 2 turnouts

  GPIO usage:

  Decoder  pins     function

  Sensor   D0 .. D7     digital sensor
           A0           analogue sensor

  Switch   D0 .. D7     output (switch)

  Turnout  D0    relais 1
           D1    current detector 1
           D2    current detector 2
           D3    not used
           D4    not used
           D5    relais 2
           D6    servo 1
           D7    servo 2
           D8    not used
           A0    not used

  ROCNET PROTOCOL

  packet payload content:
  byte 1  : groupId
  byte 2  : receiveIdH
  byte 3  : receiveIdL
  byte 4  : sendIdH
  byte 5  : sendIdL
  byte 6  : group
  byte 7  : code
  byte 8  : length
  byte 9  : data1
  byte 10 : data2
  byte 11 : data3
  byte 12 : data4

  --byte 1 only used for large network. Normally 0.

  --byte 2 only used when more than 255 decoders. Normally 0.

  --byte 3 Rocrail Server default Id is 1

  Broadcast Id = 0
  Decoder   Id = 2 ... 255   Not used for switching decoder

  --byte 4 only used when more than 255 decoders. Normally 0.

  --byte 5 Rocrail Server default Id is 1

  Decoder Id   = 2 ... 255 with restrictions as described under "addressing"

  --byte 6

  groups
  code   description     remark                     MQTT topic
  0      Host            Rocrail                    rocnet/ht
  7      Clock Fast      Clock                      rocnet/ck
  8      Sensor          Position determination     rocnet/sr
  9      Output                                     rocnet/ot


  --byte 7

  Code:  bit 7 = 0
     bit 6 and bit 5 represent Type of code
     bit 4 .. 0:  5 bit command 0 .. 31

  Type: 0 - test
  1 - request
  2 - event
  3 - reply

  Sensor

  Actions
  code description data 1  data 2  data 3  data 4  data n
  1    report      addrH¹  addrL¹  status  port    identifier (RFID)

  ¹) Address of the reporting loco.
  The sensor ID is set in the header; Sender.

  Output

  Type   Value
  switch   0
  light    1
  servo    2

  Actions
  code description data 1  data 2  data 3
  0      off       type    value   address
  1      on        type    value   address

  --byte 8 Netto number of following data bytes.

  At a speed of 200 KmH a loc runs 64 mm per second in scale H0 and 35 mm per second in scale N.
  To come to a reliable detection reaction a point sensor must be scanned at least 20 times per second in H0
  and at least 10 times per second in scale N.

  For scale H0 scan delay should be not larger than 50 miliseconds and for scale N not larger
  than 100 miliseconds. Default will be 20.

  The Wemos Module needs no 3.3V power supply. To the 5V pin external powersupply can be connected.

  Addressing:

  Addressing falls apart in a WiFi address, being an IP-address and a Rocnet address.

  Addressing:

  In the Rocnet protocol (IdH*256 + IdL) represents the Rocnet Node Number. This number ranges from 1 .. 65536.
  It represents the "Bus" number.
  Depending on the function performed the I/O pin of the decoder is addressed with "data3" for
  "output" functions or "data4" for "sensor" functions. Turnouts are controlled with an "output" function.
  The values of data3/data4 are in rocrail inserted in field "Address"

  For eltraco an I/O pin is addressed by the combination of receiveIdL and data3/data4.
  This way each individual pin of each individual decoder can be addressed.

  A second way to address an IO pin is using a "fixed" receiveIdL and discriminating by means of data3/data4.
  Using this method provides in eltraco the possibility to address 255 turnouts by a consecutive number only.
  The default receiveIdL of Rocrail is "9". This receiveIdL is used to control turnouts. These addresses are
  used by the servo-tool to adjust the servo of a turnout.

  IP-address:
  The following IP-adress range is available:
  192.168.xxx.xxx


  IP-addres: Router 192.168.xxx.251
             Servo tool 192.168.xxx.252
             Command Station 192.168.xxx.253
             Mosquitto 192.168.xxx.254

  For the decoders are available 192.168.xxx.2 - 192.168.2.250 except 192.168.xxx.9

  Smart turnout decoder:

  Each decoder controls 2 turnouts and reports occupation of them.

  Each of both turnouts is allocated a unique consecutive number out of the range 1 .. 256.
  This is the Rocrail "Address" number. The Rocrail default "Bus" number is "9". This Bus is used to control
  turnouts.

  For the turnout decoder occupation of the first turnout is reported at "Address" 1 and of the second
  turnout at "Address" 2.

  Table: Switches tab Interface - "9" is inserted into field "Bus"
         The unique number of the turnout is inserted into field "Address"
         e.g. (turnout 23 is inserted as Bus 9 Address 23)

  Table: Sensor tab Interface - "9" is inserted into field "Bus"
         The unique number of the turnout is inserted into field "Address"
         e.g. (sensor for turnout 23 is inserted as Bus 9 Address 23)

  Each of all other kinds of decoder is allocated a unique IP-address out of the range
  192.168.xxx.2 - 192.168.2.250. The last triplet is the Rocrail "Bus" number.

  Sensor decoder:
  Each decoder has eight digital and one analogue sensor.

  Each decoder is allocated a unique IP-address out of the range 192.168.xxx.2 - 192.168.2.250.
  The last triplet is the Rocrail "Bus" number.

  The sensors report using "Address" numbers 1 .. 9.

  Table: Sensor tab Interface - the last part of the IP-address is inserted into field "Bus"
         port number is inserted into field "Address"
         e.g. (192.168.0.076 sensor 5 is inserted as Bus 76 Address 5)

  Output decoder
  Each decoder has eight outputs.

  Each decoder is allocated a unique IP-address out of the range 192.168.xxx.2 - 192.168.2.250.
  The last triplet is the Rocrail "Bus" number.

  The outputs are switched using "Address" numbers 1 .. 8.

  Table: Switches tab Interface - the last part of the IP-address is inserted into field "Bus"
         The individual port number is inserted into field "Address"
         e.g. (192.168.0.201 port 3 is inserted as Bus 201 Address 3)

  During testing it turned out that move orders from Rocrail arived so fast that an ongoing movement was
  interrupted. incoming turnout orders are stored into buffer. When ongoing movement is concluded, buffer is converted
  into turnout order.

  Author: E. Postma

  September 2017

   *****/

#include <PubSubClient.h>
#include <Servo.h>
#include <stdlib.h>
#include <ArduinoOTA.h>
#include <ESP8266WiFi.h>
#include <EEPROM.h>
extern "C" {
#include "user_interface.h"
}

Servo servo[2];
WiFiClient espClient;

#define WIFI_TX_POWER 0 // TX power of ESP module (0 -> 0.25dBm) (0...85)

// do not use as turnoutNr1 or turnoutNr2: 1 and 9
static byte turnoutNr1 = 21;                               // also used in IP address decoder (check if IP address is available)
static byte turnoutNr2 = 22;
static char wiFiHostname[] = "ELTRACO-ST-21";              // Hostname displayed in OTA port
static String version = "2017-12-21";
static String decoderType = "Double turnout";
///////////////////////
/*
   Define which Wifi Network is to be used
   0 = Network 0 train room
   1 = Network 1 test room
   2 = Mobile demo layout

*/
#define WIFI_NETWORK 2

//////////////////////////// wifi network selection //////////////
#if WIFI_NETWORK == 0
static const char *ssid = "SSID0";                                          // ssid WiFi network
static const char *password = "PWD0";                                       // password WiFi network
static const char *MQTTclientId = (wiFiHostname);                           // MQTT client Id
IPAddress mosquitto(192, 168, 2, 1);                                        // IP address Mosquitto
IPAddress decoder(192, 168, 2, turnoutNr1);                                 // IP address decoder
IPAddress gateway(192, 168, 2, 1);                                          // IP address gateway
IPAddress subnet(255, 255, 255, 0);                                         // subnet mask

#endif

#if WIFI_NETWORK == 1
static const char *ssid = "SSID1";                                          // ssid WiFi network
static const char *password = "PWD1";                                       // password WiFi network
static const char *MQTTclientId = (wiFiHostname);                           // MQTT client Id
IPAddress mosquitto(192, 168, 2, 1);                                        // IP address Mosquitto
IPAddress decoder(192, 168, 2, turnoutNr1);                                 // IP address decoder
IPAddress gateway(192, 168, 2, 1);                                          // IP address gateway
IPAddress subnet(255, 255, 255, 0);                                         // subnet mask

#endif

#if WIFI_NETWORK == 2
static const char *ssid = "SSID2";                                          // ssid WiFi network
static const char *password = "PWD2";                                       // password WiFi network
static const char *MQTTclientId = (wiFiHostname);                           // MQTT client Id
IPAddress mosquitto(192, 168, 1, 254);                                      // IP address Mosquitto
IPAddress decoder(192, 168, 1, turnoutNr1);                                 // IP address decoder
IPAddress gateway(192, 168, 1, 251);                                        // IP address gateway
IPAddress subnet(255, 255, 255, 0);                                         // subnet mask

#endif
PubSubClient client(espClient, mosquitto);
//////////////////////////////////////// decoder function selection ///////////////////////////////////////////////////
static const String topicPub = "rocnet/sr";                                  // rocnet/rs for sensor
static const String topicSub1 = "rocnet/ot";                                 // rocnet/ot for turnout control
static const String topicSub2 = "rocnet/cf";                                 // rocnet/cf for servo configuration
static const String topicSub3 = "rocnet/sr";                                 // rocnet/rs for sensor
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
void loop() {
  ArduinoOTA.handle();                                                          // OTA handle must stay here in loop
  yield();

  CheckBuffer();
  ProcessOrder();
  if (configFlag == false) ServoAdjust();
  ScanSensor();

  if (!client.connected()) {                                                   // maintain connection with Mosquitto
    Reconnect();
  }
  client.loop();                                                               // content of client.loop can not be moved to function
  if (sendMsg == true) {                                                       // set sendMsg = true  to transmit message
    if (debugFlag == true) {
      Serial.println();
      Serial.print(F("Publish msg  ["));
      Serial.print(topicPub);
      Serial.print(F(" - DEC, dotted] ==> "));
      for (int index = 0 ; index < msgLength ; index++) {
        Serial.print((msgOut[index]), DEC);
        if (index < msgLength - 1) Serial.print(F("."));
      }
      Serial.println();
    }
    if (client.publish(MQTT::Publish(topicPub, msgOut, msgLength).set_qos(2)) != true) {     // message is published with qos2, highest
      Serial.println(F("fault publishing"));                                                 // guarantee for delivery of message to Mosquitto
    } else sendMsg = false;
  }
}
///////////////////////////////////////////////////////////// end of program loop ///////////////////////
/*
   SoftwareVersion

    function : display on serial monitor decoder type and sofware version

    called by: reconnect

*/
void SoftwareVersion() {
  Serial.println();
  Serial.print("\n===================================================================");
  Serial.print("\n");
  Serial.print("\n        EEEEE  LL   TTTTTT  RRR        A        CCC     OO");
  Serial.print("\n        EE     LL     TT    RR RR    AA AA     CC     OO  OO");
  Serial.print("\n        EEE    LL     TT    RRR     AAAAAAA   CC     OO    OO");
  Serial.print("\n        EE     LL     TT    RR RR   AA   AA    CC     OO  OO");
  Serial.print("\n        EEEEE  LLLLL  TT    RR  RR  AA   AA     CCC     OO");
  Serial.print("\n");
  Serial.print("\n===================================================================");
  Serial.println();
  Serial.print("\n                    decoder: ");
  Serial.println(decoderType);
  Serial.println();
  Serial.print("\n                    version: ");
  Serial.print(version);
  Serial.println();
  Serial.print("\n-------------------------------------------------------------------");
  Serial.println();
} // end of SoftwareVersion

/*

   ScanSensor

   function : read status of input pins. adjust status of sensor, generate outgoing message,
              sensorCountOff used to decide after how many scans "LOW" the sensor status is adjusted
              required for current detector
              set sendMsg = true to send message, set sendMsg = false for scan loop

   called by: loop

*/
void ScanSensor() {
  for (byte index = 0; index < sensorNr; index++) {
    if ( millis() > sensorProcessTime[index]) {
      sensorProcessTime[index] = millis() + scanDelay;
      sensorStatusOld[index] = sensorStatus[index];
      scan = !digitalRead(sensor[index]);
      if (scan == false) {
        sensorCountOff[index]++;
      }
      if (scan == true) {
        sensorCountOff[index] = 0;
        sensorStatus[index] = true;
      }
      if ((sensorCountOff[index]) > scanNegativeNr) {
        sensorStatus[index] = false;
      }
      if ((sensorStatusOld[index]) != (sensorStatus[index])) {
        sendMsg = true;
        msgOut[10] = sensorStatus[index];
        msgOut[11] = addressSr[index];
      }
    }
  }
} // end of Scansensor



/*

   CheckBuffer

   function : converts buffer into turnout order at right time

   called by: loop

*/
void CheckBuffer() {
  if (order.executed == true) {
    if (buf.orderNew == true) {
      buf.orderNew = false;
      order.in = buf.order;
      order.targetId = buf.targetId;
      order.executed = false;
      order.msgMove = false;
      order.msgStop = false;
    }
  }
} //end of CheckBuffer


/*
   ProcessOrder

   function : start action

   called by: loop
   calls    : Thrown, Straight

*/
void ProcessOrder() {
  if (order.executed == false) {
    if ((order.in == 1)) Thrown(order.targetId);
    if ((order.in == 0)) Straight(order.targetId);
  }
} // end of ProcessOrder()

/*
   Thrown

   function : move servo into thrown position
              compare current servo position with ordered position, signal start servo movement,
              switch relais in middle of servo movement, signal end of movement, set flag order executed

   called by: ProcessOrder

   calls    : txMsgMove, txMsgMoveStop

*/
byte Thrown(byte turnoutId) {
  currentPosition[turnoutId] = servo[turnoutId].read();
  if ((currentPosition[turnoutId]) != (servoPos[turnoutId][1]) && millis() >= servoMoveTime[turnoutId]) {
    if (inverted[turnoutId] == true) {
      servo[turnoutId].write((currentPosition[turnoutId]) - 1);
    } else servo[turnoutId].write((currentPosition[turnoutId]) + 1);
    servoMoveTime[turnoutId] = millis() + servoDelay[turnoutId];
    if (order.msgMove == false) {
      order.msgMove = true;
      TxMsgMove(order.targetId);
    }
    if ((currentPosition[turnoutId]) == (relaisSwitchPoint[turnoutId])) digitalWrite(relais[turnoutId], HIGH);
  }
  if ((currentPosition[turnoutId]) == (servoPos[turnoutId][1])) {
    order.executed = true;
    if (order.msgStop == false) {
      order.msgStop = true;
      TxMsgMoveStop(order.targetId);
    }
  }
} // end of Thrown

/*

   function : move servo into straight position
              compare current servo position with ordered position, signal start servo movement
              switch relais in middle of servo movement, signal end of movement, set flag order executed

   called by: ProcessOrder

   calls    : txMsgMove, txMsgMoveStop

*/
byte Straight(byte turnoutId) {
  currentPosition[turnoutId] = servo[turnoutId].read();
  if ((currentPosition[turnoutId]) != (servoPos[turnoutId][0]) && millis() >= servoMoveTime[turnoutId]) {
    if (inverted[turnoutId] == true) {
      servo[turnoutId].write((currentPosition[turnoutId]) + 1);
    } else servo[turnoutId].write((currentPosition[turnoutId]) - 1);
    servoMoveTime[turnoutId] = millis() + servoDelay[turnoutId];
    if (order.msgMove == false) {
      order.msgMove = true;
      TxMsgMove(order.targetId);
    }
    if ((currentPosition[turnoutId]) == (relaisSwitchPoint[turnoutId])) digitalWrite(relais[turnoutId], LOW);
  }
  if ((currentPosition[turnoutId]) == (servoPos[turnoutId][0])) {
    order.executed = true;
    if (order.msgStop == false) {
      order.msgStop = true;
      TxMsgMoveStop(order.targetId);
    }
  }
} // end of Straight

/*
   ServoAdjust

   function : adjust straight and thrown position of servo. positions sent by servo tool.

   called by: loop

*/
void ServoAdjust() {
  if ((servoAngle) != (servoAngleOld)) {
    Serial.print("angle: ");
    Serial.println(servoAngle);
    servo[servoId].write(servoAngle);                           // servo takes position sent by servo tool
    servoAngleOld = servo[servoId].read();
  }
  if ((ackStraight == 1) && (ackThrown == 0)) {
    servoPos[servoId][0] = servoAngle;                          // angle accepted when ack received
  }
  if ((ackThrown == 1) && (ackStraight == 0)) {
    servoPos[servoId][1] = servoAngle;                          // angle accepted when ack received
  }
  if ((ackStraight == 1) && (ackThrown == 1)) {                 // cycle concluded when both acks are received
    if (debugFlag == true) {
      Serial.println();
      Serial.print("Servo Turnout address: ");
      Serial.print(addressTu[servoId]);
      Serial.print(" angle 1 - ");
      Serial.print(servoPos[servoId][0]);
      Serial.print(" angle 2 - ");
      Serial.print(servoPos[servoId][1]);
      Serial.println();
    }
    EEPROM.write ((servoId * 2), servoPos[servoId][0]);         // write values in EEPROM
    EEPROM.write ((servoId * 2 + 1), servoPos[servoId][1]);
    EEPROM.commit();
    delay(200);
    memset(msgOut, 0, sizeof(msgOut));
    msgOut[0] = addressTu[servoId];
    msgOut[4] = 1;
    sendMsg == true;
    configFlag = true;
    ReadEEPROM();
    if (debugFlag == true) {
      Serial.println();
      Serial.println("servo adjusted");
      Serial.println();
    }
    ackStraight = 0;
    ackThrown = 0;
  }
} //end of servoAdjust

/*
   WriteEEPROM

   function : write initial servo values to EEPROM

   called by: setup
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

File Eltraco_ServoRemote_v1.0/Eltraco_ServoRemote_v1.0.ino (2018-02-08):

/*
    
        This software is no longer supported. The servo remote is discarded.
        This function is incorporated into the "Elatraco configuration website"
        on each decoder.
    
  changelog:
  "2018-02-03" website for configuration decoder added. Single software package.
    
  changelog:
  "2017-12-21" Software version display added
            
  dec 2017-2
  "char" for numbers is WRONG!
  change to byte

  dec 2017:
  new MQTT library. supports qos2. link for library: https://github.com/Imroy/pubsubclient
  Length of MQTT outgoing message equal to Rocnet message length.
  "yield()" in loop.
  display of published and received messages on serial monitor harmonised.
  change "byte" to "char"
  reduce TX power


  Eltraco_Servo Remote v1.0
  Ready for publication

  /*************************************************************************************

  This software constitutes a Servo adjustment tool.
  Address of decoder is read from 8 dipswitches.
  Target platform is the Wemos D1 mini module.

  Message structure:
  byte 0: decoderId of Decoder
  byte 1: StraightPos    1 .. 255
  byte 2: StraightAck       1
  byte 3: ThrownAck         1

  The address of the servo is selected with a 8-bit dipswitch.
  During selection process LED is continuously ON.

  The address is acknowledged with the "ack" push button connected to 5.
  LED flashes 3 times.

  The messages with the angle for the servo are generated by turning the knob of a potmeter.
  The mid point connected to A0.
  The left point connected to 3.3V and the right point connected to GND.

  The "ack" button is used to confirm the angle for the "straight" position of the turnout.
  LED flashes 3 times.

  The next message for the servo is generated with the potmeter.

  The "ack" button is used to confirm the angle for the "thrown" position of the turnout.
  LED flashes 3 times.

  Use the "ack" button to conclude the sequence. The address selection process starts again.


    y = (x >> n) & 1;    // n=0..15.  stores nth bit of x in y.  y becomes 0 or 1.
    x &= ~(1 << n);      // forces nth bit of x to be 0.  all other bits left alone.
    x |= (1 << n);       // forces nth bit of x to be 1.  all other bits left alone.
    x ^= (1 << n);       // toggles nth bit of x.  all other bits left alone.
    x &= (1<<(n+1))-1;   // leaves alone the lowest n bits of x; all higher bits set to 0.
    x = ~x;              // toggles ALL the bits in x.

  IP-addres: Mosquitto 192.168.0.254
             Router 192.168.0.253
             Servo tool 192.168.0.252


  Author: E. Postma

  September 2017

*****/

#include <PubSubClient.h>
#include <ESP8266WiFi.h>
#include <SoftwareSerial.h>
#include <EEPROM.h>
#include <ESP_PCF8574.h>

extern "C" {
#include "user_interface.h"
}

#define SDA_PIN D1
#define CLK_PIN D2
#define PCF8574_ADDRESS (0x20)

ESP_PCF8574 dipSwitch;


WiFiClient espClient;

#define WIFI_TX_POWER 0 // TX power of ESP module (0 -> 0.25dBm) (0...85)

char wiFiHostname[] = "ServoTool";                           // Hostname displayed in OTA port

static const String topicPub = "rocnet/cf";                   // rocnet/cf for servo tool
static const String topicSub = "rocnet/cf";                   // rocnet/cf for servo tool
static String version = "2017-12-21";
static String decoderType = "Servo tool";
///////////////////////
/*
   Define which Wifi Network is to be used
   0 = Network 0 train room
   1 = Network 1 test room
   2 = Mobile demo layout

*/
#define WIFI_NETWORK 2
//////////////////////////// wifi network selection //////////////
#if WIFI_NETWORK == 0
static const char *ssid = "SSID0";                                       // ssid WiFi network
static const char *password = "PWD0";                                    // password WiFi network
static const char *MQTTclientId = (wiFiHostname);                        // MQTT client Id, differs per decoder, to be set by user
IPAddress mosquitto(192, 168, 2, 1);                                     // IP address Mosquitto
IPAddress decoder(192, 168, 2, 252);                                     // IP address decoder
IPAddress gateway(192, 168, 2, 1);                                       // IP address gateway
IPAddress subnet(255, 255, 255, 0);                                      // subnet mask
#endif

#if WIFI_NETWORK == 1
static const char *ssid = "SSID1";                                       // ssid WiFi network
static const char *password = "PWD1";                                    // password WiFi network
static const char *MQTTclientId = (wiFiHostname);                        // MQTT client Id, differs per decoder, to be set by user
IPAddress mosquitto(192, 168, 2, 1);                                     // IP address Mosquitto
IPAddress decoder(192, 168, 2, 252);                                     // IP address decoder
IPAddress gateway(192, 168, 2, 1);                                       // IP address gateway
IPAddress subnet(255, 255, 255, 0);                                      // subnet mask
#endif

#if WIFI_NETWORK == 2
static const char *ssid = "SSID2";                                       // ssid WiFi network
static const char *password = "PWD2";                                    // password WiFi network
static const char *MQTTclientId = (wiFiHostname);                        // MQTT client Id
IPAddress mosquitto(192, 168, 1, 254);                                   // IP address Mosquitto
IPAddress decoder(192, 168, 1, 252);                                     // IP address decoder
IPAddress gateway(192, 168, 1, 251);                                     // IP address gateway
IPAddress subnet(255, 255, 255, 0);                                      // subnet mask

#endif
PubSubClient client(espClient, mosquitto);

static boolean debugFlag = true;
static boolean caseFlag = false;

///////////////////////////////////////////////////////////////////////////////////////


static const int msgLength = 4;                              // message number of bytes
static byte msgOut[msgLength];                               // outgoing messages
static byte msgFlag = 0;                                     // control sending message
static byte sendNr = 1;
static byte sendCntr = 0;

static boolean dip[8];                                       // dipswitch
static byte const Led = D0;                                  // acknowledge LED
static byte const ackButton = D5;                            // acknowledge button
static byte const potPin = A0;                               // potentiometer read pin

static int potVal = 0;                                       // pot meter value
static byte potValOld = 0;
static byte butVal = 0;                                      // button value

static byte decoderAddress = 0;
static byte decoderAddressOld = 0;
static boolean addressSelected = false;
static boolean msgPotSent = false;
static boolean msgStraightSent = false;
static boolean msgThrownSent = false;
static byte confirmCount = 0;
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

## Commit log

2017-10-01 Sensor decoder
    Working version of the sensor decoder. Eight digital and one analogue
    sensors signal occupancy to Rocrail. Available sensors are hall sensor
    and single current detector sensor.
2017-10-01 Eagle files for Eltraco
    [Sensor Decoderv0.5.GBL, Sensor Decoderv0.5.GBO, Sensor Decoderv0.5.GBP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]
2017-10-02 DCC++ booster running on Arduino Nano
    The original software has been adapted to run on Arduino Nano with
    related motor shield.
    The aim is to operate this booster via WiFi and MQTT.
2017-10-23 Eagles files for hall sensor connector
    [Hall_Sensor.GBL, Hall_Sensor.GBO, Hall_Sensor.GBP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]
2017-12-19 MQTT broker details retrieved from Rocrail or default data used
    Liviu developed a software module to retrieve MQTT broker data from
    Rocrail. This module is slightly adapted and incorporated.
    [Eltraco_Receiver_v1.0.ino]
2017-12-20 Replace "char" by "byte" for numbers
    [Eltraco_Clock_v1.0.ino, Eltraco_Receiver_v1.0.ino, Eltraco_Sensor_v1.0.ino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]
2017-12-22 Software version display added with internal clean-up
    Software versioning has changed. Display of current version on serial
    monitor. Internal clean-up.
2018-01-03 Incoming switch order now correct
    Wrong byte of incoming payload corrected.
    [Eltraco_Switch_v1.0.ino]
2018-01-04 One of two no PCB traces. Corrected.
    [Sensor Decoderv0.5.brd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]
2018-02-08 Major change in software
    The separate software packages have been combined into one Eltraco
    package. Configuration is done by means of the built-in “Eltraco
    configuration website”. Servo adjustment is done via the same website.
    The “servo tool” is abandonned.
    Further more a new decoder is introduced, the single turnout decoder
    with four connectors for external sensors.
    [ServoToolv04.brd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]
2018-02-08 ESP8266WebServer server(80); inserted
    ESP8266WebServer server = ESP8266WebServer(80); replaced by
    ESP8266WebServer server(80);
2018-02-09 New version PCB files and extra PCBs
    Value of components printed on PCB. Current sensor, hall sensor and
    relais add-on PCB added
    [Current Sensor v0_6.GBL, Current Sensor v0_6.GBO, Current Sensor v0_6.GBP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]
2018-02-11 Reboot inserted after "wifi restart" selection in configuration webpage
2018-02-15 Web page "servo adjustment" updated
2018-04-06 Incorporation off minimum positive scan pulse duration of 300 milllis
    The Hall sensor generates a puls of only several ms. This is to short
    for Rocrail. Every positive scan pulse is has now an adjustable
    duration. Default is 300 ms.
